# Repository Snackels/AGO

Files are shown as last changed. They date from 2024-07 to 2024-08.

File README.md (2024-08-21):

# Documentation for WRO Future Engineer 2024
by Team *YBR-AGO*



<p align="center">
  
</p>
<p align="center">
<b>By Yothinburana School Robot Club</b>
</p>
<br><br><br><br>

## Our works (Youtube Links): 
Without obstacle
**https://youtu.be/OX0P1ySq7O0?si=p41OlnyZ8GQXAvJI**

In this round, our strategy is to map the distance between the robot and the wall to be 30 CM. To start the robot, we place it on the track. Then we will open the switch to turn the robot on. After the switch is pressed, all servos will return to default position to ensure that the robot has the same value everytime. After that we will press the button at the back of our robot to start it. The ultrasonic servo will turn to the right to keep robot away from the wall. The robot will walk straight until the light sensors see the blue and red line on each corner of the track. The red sensor is used for detecting the blue line which indicate that the robot need to turn left. While blue sensor is used for both blue and red line. If the robot sees the red line first, it will turn right. We count the color line for 12 times to make sure that the robot has completed 3 laps around the track. After that line we will use timer to drive into parking position.

With obstacle

<br>

### This Github repository contains:
  - [About our team](#about-our-team)
  - [Robot Design](#robot-design)
  - [Electric Circuit And Flowchart](#electric-circuit-and-flowchart)
  - [Program Explanation](#program-explanation)

# **About our team.**
<p align="center">
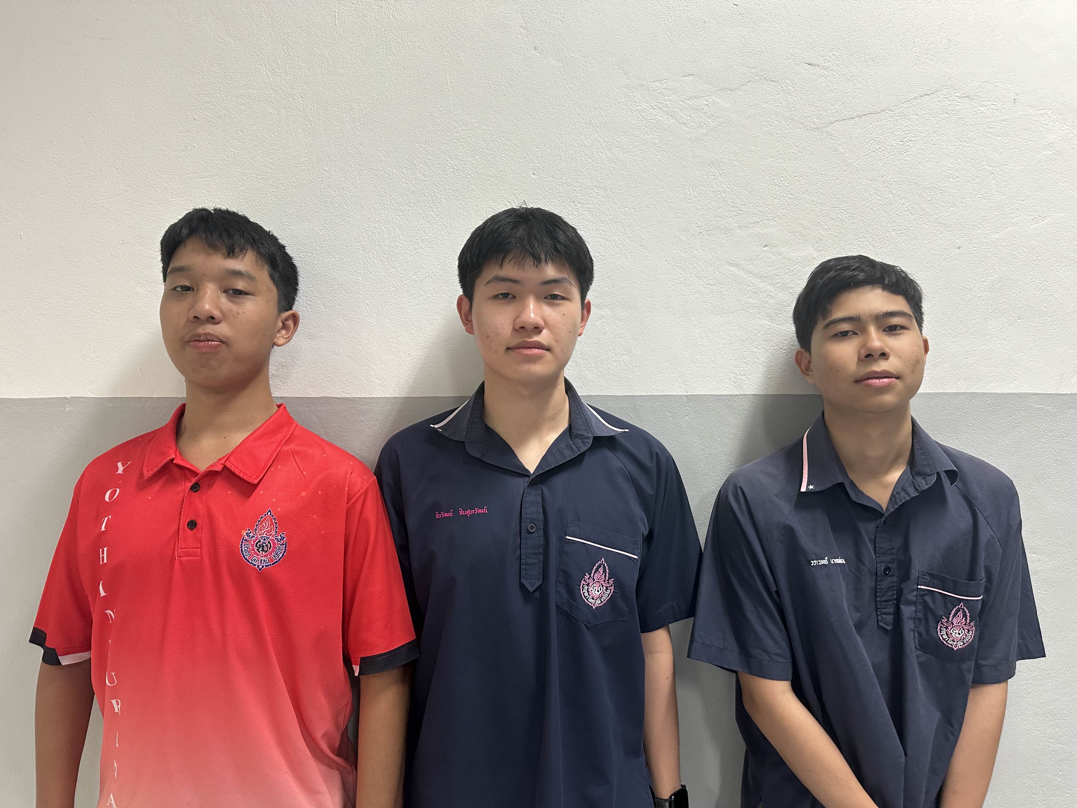
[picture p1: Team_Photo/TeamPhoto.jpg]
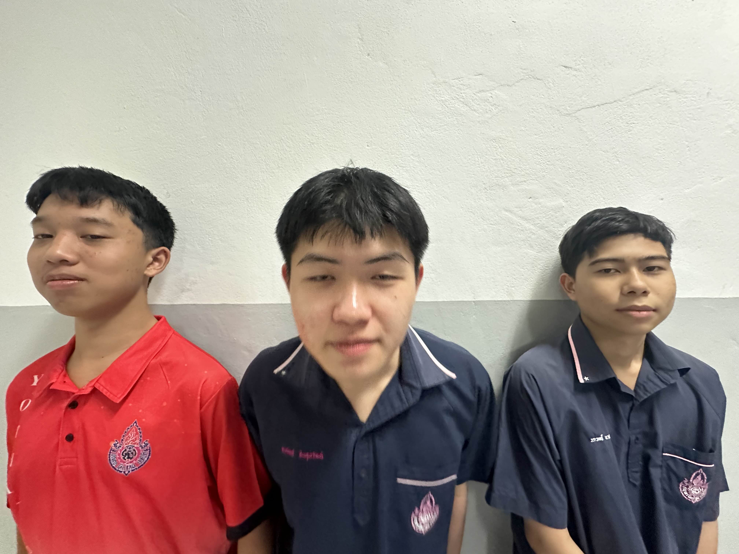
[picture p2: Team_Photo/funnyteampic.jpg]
   
</p>
<p align="center">

*YBR-AGO* comprises three students from Yothinburana School. Our team consists of two members from year 11 and one from year 10. Last year, Vichaiwat and Vorawet secured first place in Thailand national stage with team YBR-GPA4.0 while Chaiwat came in second with the team YBR-BOO. We all made it into international round as Thailand representative. Sadly, Vichaiwat and Vorawet in team called Sunflower secured 7th place and Chaiwat in Zenith secured the 8th. Now we know what we should do to prevent that from happening again and try our best to win that first place.

Here are the team members from left to right.

1. Vichaiwat Koonsap, 16 years old.

2. Chaiwat Chinsupawat, 15 years old.

3. Vorawet Narkglom, 16 years old.

# **Robot Design.**
### The Robot

Designing a robot for this competition is sometimes hard. We need to design it to be compact, lightweight, durable, and have all the functions we need. The robot must be four-wheeled with a steering function on either front or back wheel, which is why we need to be careful to pick the components. After we select all the components we need, then we think about how to put them all together. We came up with using Lego Technic parts. We spent a lot of time designing it to be within the size regulation. 

Designing a robot using Lego parts is also not easy since we need to think about everything. Every part we put in includes weight, which makes the robot slower. We failed a few times before coming up with the design we use now. After finishing designing, we combined it with other components to see the result. he robot's color also shouldn't be green and red since the camera can confuse it with the obstracle.

For the design, we placed the gyro around the middle-top of the robot to get the most accurate output, while the camera was positioned at the front of the gyro to detect objects quickly.

Our robot has two servos, one on the bottom front and one on the top front. The bottom front servo is used to steer the wheel. Then, we added a top servo that rotates our ultrasonic. We use an ultrasonic to keep our robot out of the wall. Finally, we place our motor at the bottom back of the robot, and to ensure that it drives both wheels at the back, we use a gear differential from Lego. 

Here is what our robot looks like without the components.

<image src="https://github.com/Snackels/AGO/blob/main/Robot/3D/Robot%20render.png" width = "400">

<br>

This is how to make our robot in timelapse. It shows inside of the robot of where and how to put the motor and differential.
<div align="center">
    Robot Car Assemble
</div>

<br>

### Our robot components
  
   ### Movement Parts
   
- ## **Driving motor** : Power functions Large-motor made by LEGO™.
<image src="https://github.com/Snackels/FutureEngineer2024_YBR_AGO/blob/main/Robot/Parts/Motor.png" width = "400">
It's a simple motor, and we chose this motor because of its easy connection to our robot and its cost-effectiveness. This motor is small yet powerful. and it is the perfect size for our robot. The motor comes with a dedicated port for Lego. So, we modified it to make it able to connect to the board. 

### Electrical Specifications

| Specification | Value |
|---|---|
| Voltage | 9 V |

### Mechanical Specifications

| Specification | Value |
|---|---|
| Speed | 390 rpm  |
| Maximum torque | 40 Ncm |

<br><br>

- ## **Servo** : GEEKSERVO 2kg 360 Degrees servo.
<image src="https://github.com/Snackels/FutureEngineer2024_YBR_AGO/blob/main/Robot/Parts/Servo%201.png" width = "400">
We use this servo for steering the robot and employ an ultrasonic sensor for rotation. This servo is compatible with LEGO, making it easy and convenient to build the robot by just putting studs in the hole on the side. We like how you can connect two axles to the dual outputs on this servo so you can power two wheels or gears, or mount the servo securely inside articulated limbs and other contraptions. Additionally, the gears inside these servos will 'slip' when the blocking load is too high instead of jamming, helping avoid damage to your servos and boards.

The wires are a standard servo pinout - 
-	Red - positive
-	Brown - negative
-	Yellow - data

### Electrical Specifications

| Specification | Value |
|---|---|
| Working voltage | 3.3V~6V  |
| Rated voltage | 4.8V |
| Rated current | 200mA |
| Stall current | 700mA |
| Sliding current | 450mA |

- ## **Differential** : Technic, gear differential with inner tabs and closed center, 28 bevel teeth
<image src = "https://github.com/Snackels/FutureEngineer2024_YBR_AGO/blob/main/Robot/Parts/Gear_3%20(1).png" width = "400">
This part ensure that both wheels have the power from the motor, which makes the robot drive forward. This part has gear teeth on the side, which are connected to the gear we put on the motor earlier, and then we put 3 small gears inside the differential. The differential is attached to the main body using an axle from the wheel.

<br><br>

- ## **Wheel** : Lego 49.5 × 20 tire and 30 × 20 rim
<image src = "https://github.com/Snackels/FutureEngineer2024_YBR_AGO/blob/main/Robot/Parts/Wheel%20(1).png" width = "400">
There are a lot of wheels to select. We chose this one because of it's size. If the wheels are too small, it reduces the speed due to the lack of rotation. But if the wheels are too big, it makes the robot slower and harder to control. With the combination of the motor and the wheels, the robot can maintain the speed we can control.

<br><br>

 ### Controller
- ## **Microcontroller Board** : Arduino Mega 2560 R3
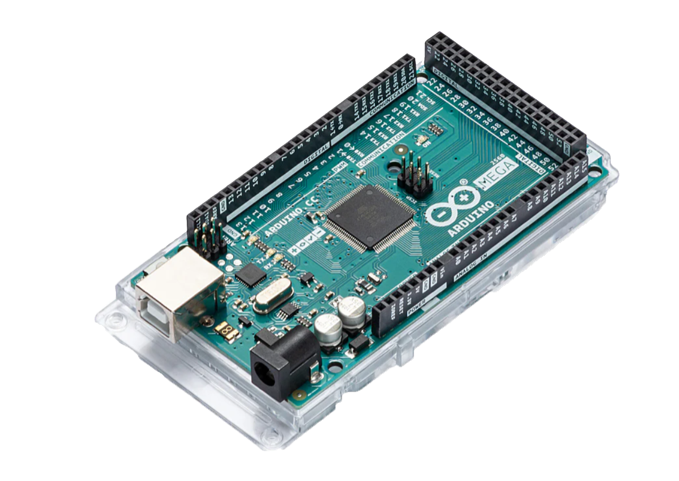
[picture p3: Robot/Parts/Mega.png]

This part is like a brain of our body. It's job is to store all the program of our robot from the computer, every components in the robot comes through here. We chose this board because of it's connection port, it contains tons of ports that we want such as 3 UART port. We used Arduino Uno last year, but the problem is there's not enough port for OpenMV and GY-25. But there's some disadvantage in this board. Because this board has a lot of connection port, it comes with weight and size. It's almost 2 times longer than the UNO. And that makes the robot long and heavy.

| Specification | Value |
|---|---|
| Microcontroller | ATmega2560 |
| Operating Voltage | 5V |
| Input Voltage (recommended) | 7-12V |
| Input Voltage (limit) | 6-20V |
| Digital I/O Pins | 54 (15 provide PWM output) |
| Analog Input Pins | 16 |
| DC Current per I/O Pin  | 20 mA |
| DC Current for 3.3V Pin | 50 mA |
| Flash Memory | 256 KB (8 KB used by bootloader) |
| SRAM | 8 KB |
| EEPROM | 4 KB |
| Clock Speed | 16 MHz |
| LED_BUILTIN | 13 |
| Length | 101.52 mm |
| Width | 53.3 mm |
| Weight | 37 g |

Additional information about UART:
UART operates by transmitting data as a series of bits, including a start bit, data bits, an optional parity bit, and stop bit(s). Unlike parallel communication, where multiple bits are transmitted simultaneously, UART sends data serially, one bit at a time. As the name reveals the protocol operates asynchronous which means that it doesn't rely on a shared clock signal. Instead, it uses predefined baud rates to determine the timing of data bits.

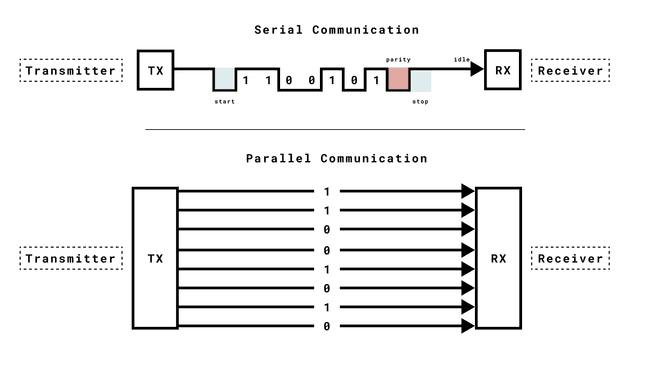
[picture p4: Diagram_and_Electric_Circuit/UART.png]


Our robot has serial1 and serial3, serial1 is connected to compass while serial3 is connected to OpenMV camera. They are connected to the UART port on the Arduino mega.

<br><br>

- ## **Sensor Shield** : Gravity IO Sensor Shield For Arduino Mega Due
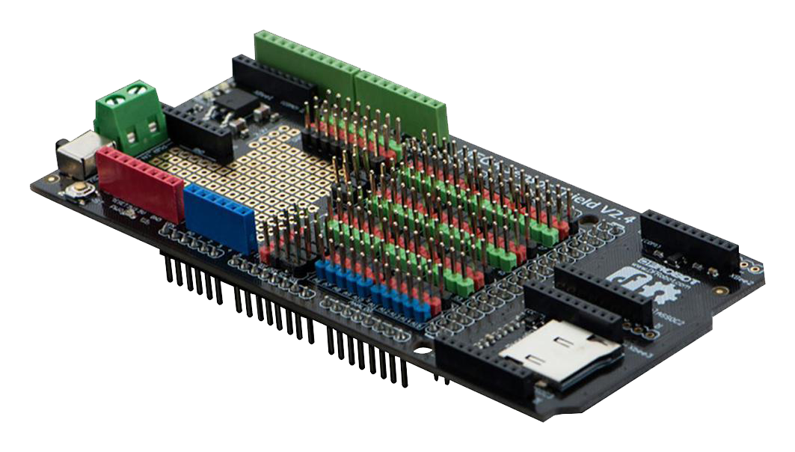
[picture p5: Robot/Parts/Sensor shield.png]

This part is an extension of the board. It is where ultrasonic, light sensors, button sensors, camera, compass, and servos go. It has alot of connection pin which can be used for each components. But with that it also come with a very long design. Make it hard to design where to place it on robot.

| Specification | Value |
|---|---|
| Compatibility | Most Arduino shields |
| Compatible Boards | Arduino Mega boards, DFRobot megaADK, Arduino megaADK |
| Extended TTL Connection Pins | Four Serial ports |
| Prototyping Area | DIP prototyping area for additional modules or components |
| Xbee Slots | 3 |
| microSD Slot | 1 |
| Power Switch | Between Arduino Mega or external power |
| Size | 125 x 57 mm (4.92 x 2.24") |

<br><br>

- ## **Motor Shield** : Gravity 2x2A Motor Shield for Arduino Twin
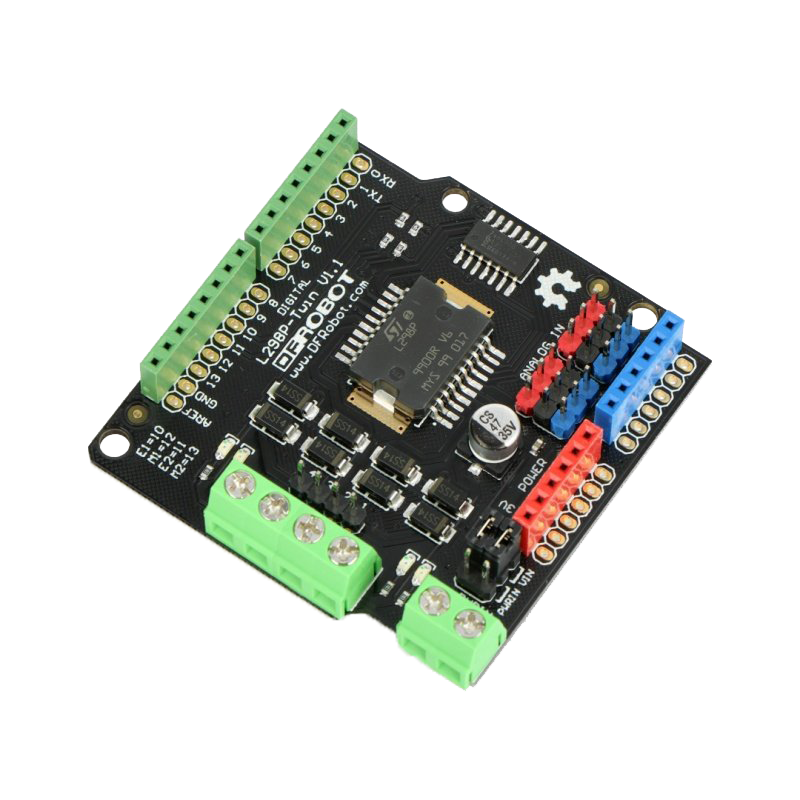
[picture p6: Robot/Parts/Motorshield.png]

This part is also an extension of the board. It makes the connection between the board and motor easier. We connect the pin with the top of sensor shield.

| Specification | Value |
|---|---|
| Motor Driven Voltage | 4.8V to 35V |
| Output Current | Up to 2A/channel |
| Total Power Dissipation | 25W (T=75℃) |
| Driven Structure | Dual full-bridge driver |
| Driven Power Port | External power terminal, or VIN from Arduino |
| Driven Output Port | 2 channel screw terminals, or male PIN headers |
| Control Port | 4 TTL compatible digital signals (Digital 10-13) |
| Operation Temperature | -25℃ to 130℃ |
| Shield Size | 56x57mm (2.20x2.24") |

<br><br>

### Power Management And Inspection
- ## **Camera** : OpenMV H7 R1
<image src="https://github.com/Snackels/AGO/blob/main/Robot/Parts/OpenMV%20cam.png" width = "400">
This component is very important for avoiding obstacle. It can detect red and green obstacle from distance to avoid crashing into it. The OpenMV also comes with it's own microcontroller. Making the robot locate and think faster when see the obstacle. The OpenMV also comes with GLCD screen at the back of it to display what the camera see. This camera can be coded with MicroPython. Additionally, this camera wires are connected with the sensor shield.

#### STM32H743VI Specifications

| Specification | Value |
|---|---|
| **Processor** | STM32H743VI ARM Cortex M7 |
| **Clock Speed** | 480 MHz |
| **SRAM** | 1 MB |
| **Flash Memory** | 2 MB |
| **I/O Voltage** | 3.3V (5V tolerant) |
| **Number of I/O Pins** | 10 |

#### Interfaces

| Specification | Value |
|---|---|
| **USB** | Full-speed USB (12 Mbps) interface |
| **μSD Card Socket** | Capable of 100 Mbps read/write |
| **SPI Bus** | Up to 80 Mbps |
| **I2C Bus** | Up to 1 Mbps |
| **CAN Bus** | Up to 1 Mbps |
| **Asynchronous Serial Bus** | Up to 7.5 Mbps |

#### Analog

| Specification | Value |
|---|---|
| **ADC** | 12-bit |
| **DAC** | 12-bit |

#### Control

| Specification | Value |
|---|---|
| **Servo Control Pins** | 3 I/O pins |
| **Interrupts and PWM** | Available on all I/O pins |

#### LEDs

| Specification | Value |
|---|---|
| **RGB LED** | Yes |
| **High Power IR LEDs** | Two 850nm |

#### Camera Module

| Specification | Value |
|---|---|
| **Default Sensor** | OV7725 |
| **Resolution** | 640x480 |
| **Modes** | 8-bit Grayscale at 75 FPS, 16-bit RGB565 (75 FPS above 320x240, 150 FPS below 320x240) |
| **Lens** | 2.8mm, M12 mount |
| **Additional Modules** | Global Shutter Camera, FLIR Lepton Adapter |

#### Power

| Specification | Value |
|---|---|
| **Battery Connector** | Compatible with 3.7V LiPo batteries |

  <br><br>

- ## **Ultrasonic sensor** : Gravity URM 09 ultrasonic distance sensor.
<image src="https://github.com/Snackels/AGO/blob/main/Robot/Parts/Ultrasonic.png" width = "400">
The ultrasonic sensor plays a vital role in guiding the robot's navigation by accurately detecting distances between the robot and potential obstacles. Its precision in measuring distances ensures that the robot can maneuver and make informed decisions to navigate its path safely and effectively, avoiding collisions and maintaining its course.

### Electrical Specifications

| Specification | Value |
|---|---|
| Supply Voltage | 3.3~5.5V DC |
| Operating Current | 20mA |

### Performance Specifications

| Specification | Value |
|---|---|
| Operating Temperature Range | -10°C to +70°C |
| Measurement Range | 2cm to 500cm (can be set) |
| Resolution | 1cm |
| Accuracy | 1% |
| Frequency | 50Hz Max |

<br><br>

- ## **7.4 voltage Lipo-Battery** : 7.4 voltage 2 cell Lipo-Battery.
<image src="https://github.com/Snackels/AGO/blob/main/Robot/Parts/Battery.png" width = "400">
The battery provides the power for our robot. This battery is very lightweight and compact to fit into the robot since the robot is very small. And it is also able to connect to our controller board. We calculated the amount of mAh that is enough to power our robot for 1-2 hours before recharged.

### Specification

| Specification | Value |
|---|---|
| 2 cells Voltage | 7.4V |
| Capacity | 1100mAh 30C |
| Charging Current | Up to 5 times the capacity (5C) |
| Connectors | JST type, easily disconnectable |

<br><br>

- ## **Light Sensor** : Virus III by Design By Sopon and ZX-03 By INEX
<image src = "https://github.com/Snackels/AGO/blob/main/Robot/Parts/Red%20sensor.png" width = "300">
Virus III
<image src = "https://github.com/Snackels/FutureEngineer2024_YBR_AGO/blob/main/Robot/Parts/Blue%20sensor.png" width = "300">
ZX-03

<br><br>

The color sensors play an important role in both rounds, as we use them for line detection. There are 2 lines with different colors in the corner of the race field, which is why we use 2 different colors of the color sensor, blue and red. The blue color sensor is used for detecting both colors, while the red color sensor is only used for the blue line.

<br><br>

- ## **GyroCompass** :GY-25
A gyro is a component that enables a robot to determine its orientation and turn in the appropriate direction. We chose this gyro sensor specifically because of how effective it is. It also comes in a very small
size to attach to our robot.

<image src = "https://github.com/Snackels/AGO/blob/main/Robot/Parts/GyroCompass.png" width = "400">

### Specification

#### Power and Communication

| Specification | Value |
|---|---|
| Power supply | 3-5V (internal low dropout regulator) |
| Used Chip | MCU+MPU6050 |
| Communication mode | Serial communication (baud 9600, 115200), IIC communication |
| Operating Current | 15 mA |

#### Angular Measurement

| Specification | Value |
|---|---|
| Angular Resolution | 0.01° |
| Direct Data | YAW ROLL PITCH |
| Measuring range of axes | -180 to +180 degrees |
| Resolution | 0.01 degrees |
| Frequency Response | 100Hz (115200bps) |
| Operating Temperature | -20 to 85°C |

<br><br>

- ## **Touch Sensor** : ZX-Switch01 by INEX
This button gives us an easier way to start the robot. Since the controller board doesn't come with switches. So we found this button that could be attached to the frame outside the board using bolt. 

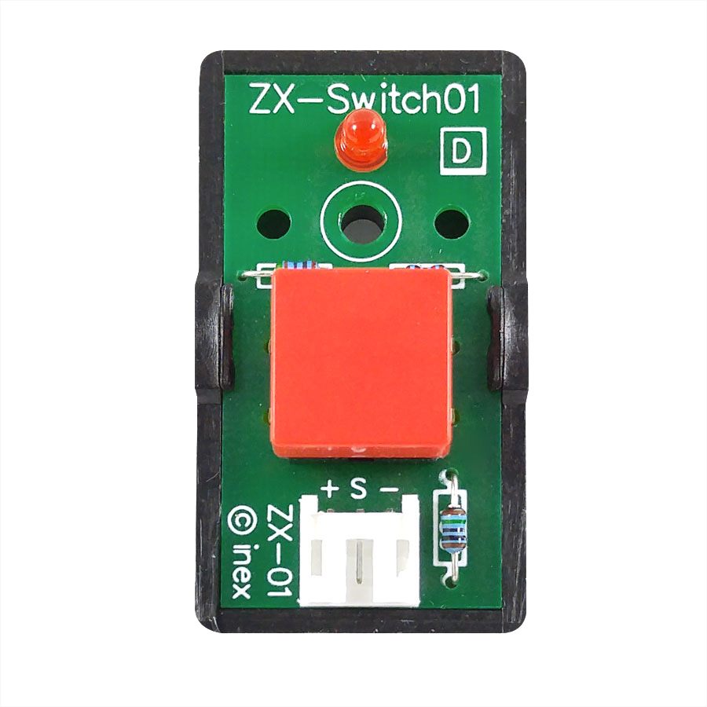
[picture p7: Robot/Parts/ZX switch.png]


<br><br>

- ## **On/Off Switch** : SPST ON/OFF Switch 2 Pin Rocker Switch DC 125/250V
This switch is for cutting the power from the battery to the robot. The regulation states that before starting the robot, the power must be cut off. That's when this switch came in. To use this switch we solder red wire(Positive pole) to the switch on 1 side for input. Then another solder red wire for output on the opposite side. You can put the black wire(Negative pole) straight into the step down. When the switch is turned on, the power from the battery will direct into the stepdown and then the robot. 

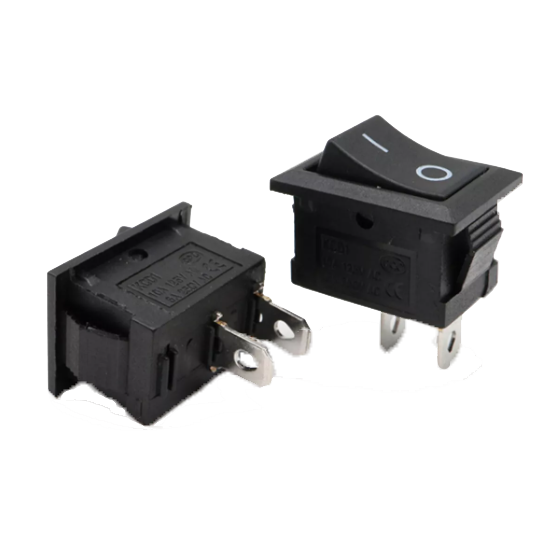
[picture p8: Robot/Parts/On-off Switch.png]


<br><br>

- ## **Step-down** : HW-360 V6.0
This is a step-down DC-DC module. It comes with a status indicator light, a display screen that shows the voltage meter, and self-calibration of the voltage meter. The electrical voltage has an error of 0.05 V, with a measuring range of 0–40 V. We need this step down to show us how long until we need to recharge the battery.

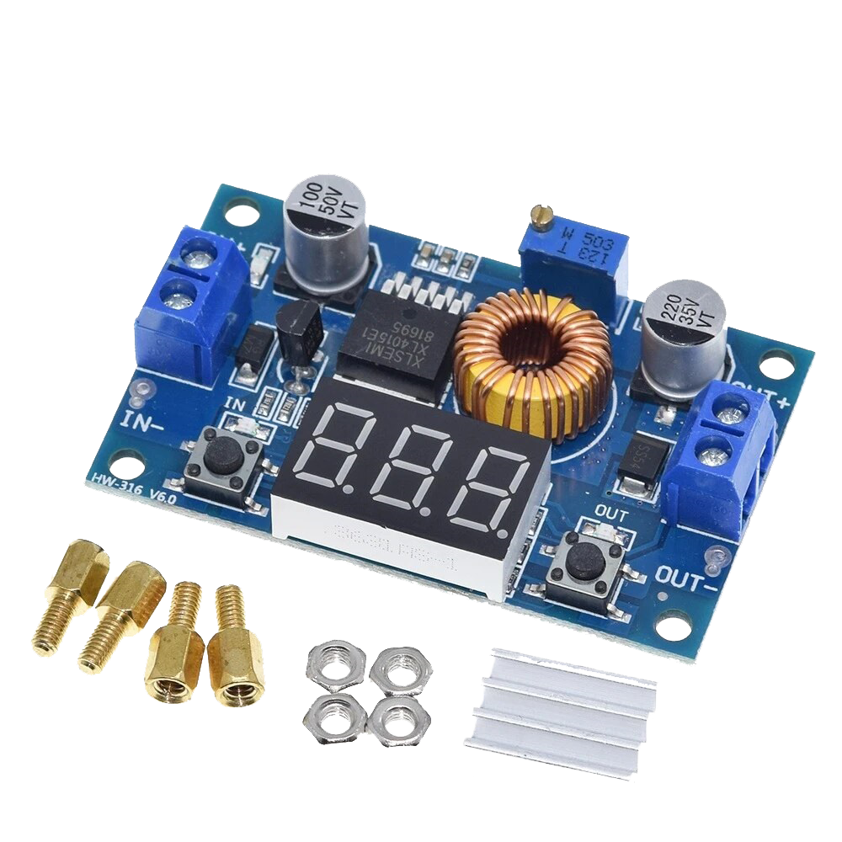
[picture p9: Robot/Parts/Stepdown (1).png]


<br><br>

### Specification

#### Input

| Specification | Value |
|---|---|
| Input voltage | DC 4.0 ~ 38V |

#### Output

| Specification | Value |
|---|---|
| Output voltage | DC 1.25V ~ 36V continuously adjustable |
| Output current | Max 5A |
| Output power | Up to 75W |

#### Measurements

| Specification | Value |
|---|---|
| Voltmeter error | ± 0.05V |
| Measure range | 0 ~ 40V |

#### Performance

| Specification | Value |
|---|---|
| Conversion efficiency | Up to 96% |
| Load regulation | S (I) ≤ 0.8% |
| Voltage Regulation | S (u) ≤ 0.8% |

<br><br>

**This is 3D model of our robot to show what our robot looks like with the components.**
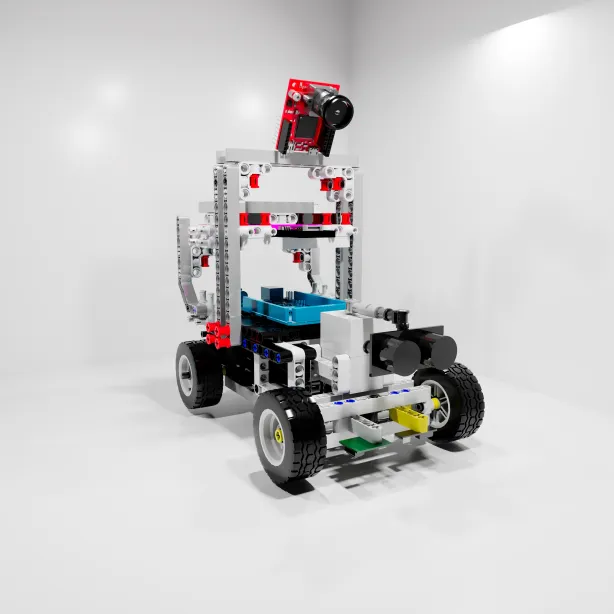
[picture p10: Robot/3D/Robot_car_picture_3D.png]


# **Electric Circuit And Flowchart**

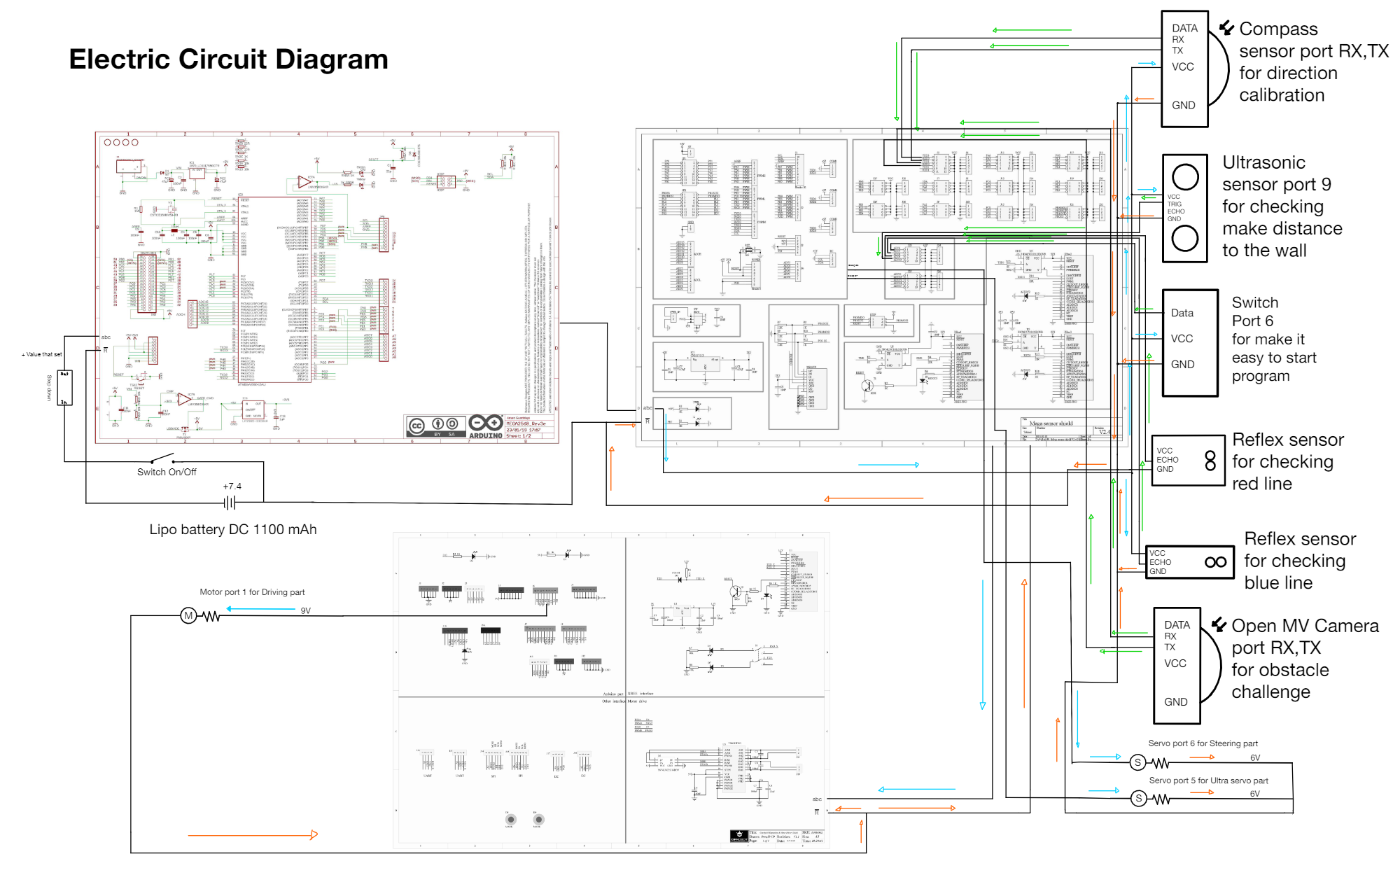
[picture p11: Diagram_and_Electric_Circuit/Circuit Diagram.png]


This is the electric diagram of our robot, showing where the wires go from the components to the board.

<br><br>

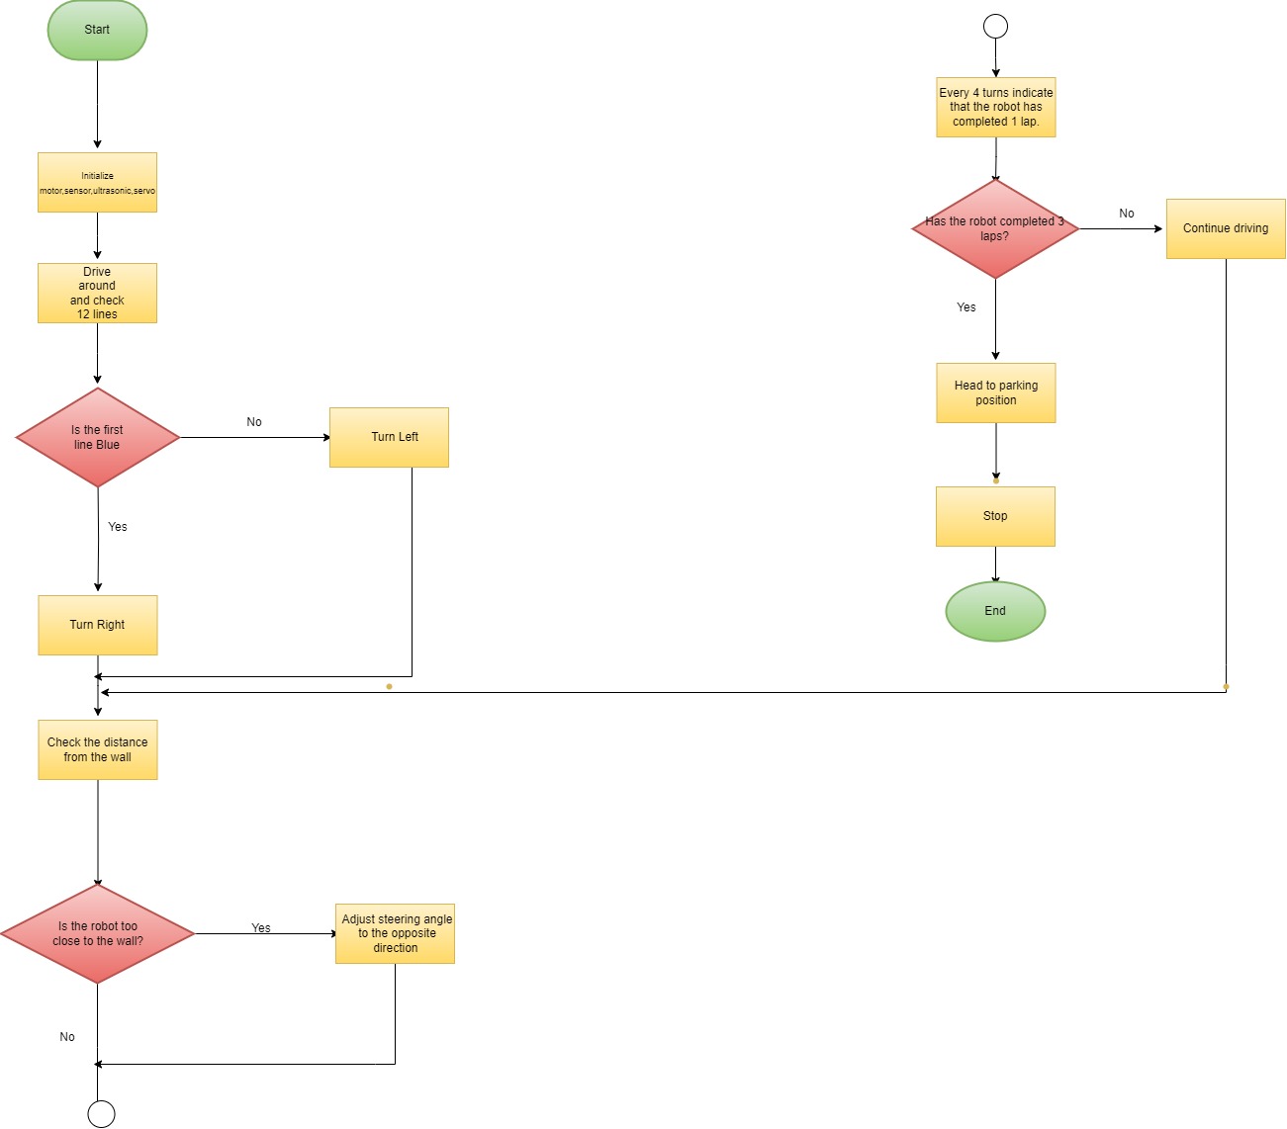
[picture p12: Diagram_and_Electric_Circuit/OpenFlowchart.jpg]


Our robot open challenge flowchart. In this round, our robot must complete 3 laps around the track within 3 minutes.

<br><br>

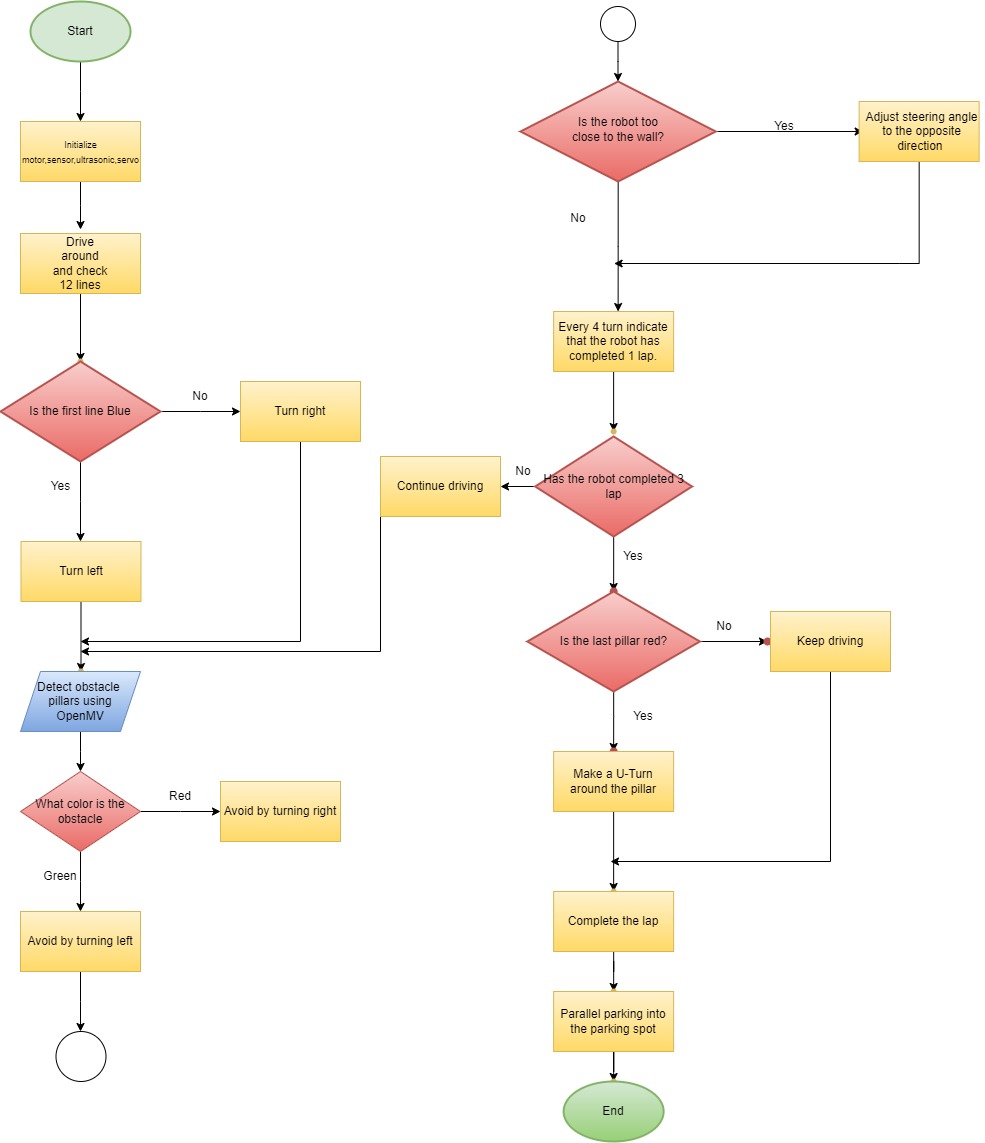
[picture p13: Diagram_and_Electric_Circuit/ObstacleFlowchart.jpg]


This flowchart shows how our robot works in obstacle challenge. 

<br><br>

 # **Program Explanation**

We have developed two programs for our upcoming competition. Each program is designed for a different round - the open challenge and the obstacle challege. The first program includes two subprograms that are also included in the program for the obstacle challenge. Each subprogram is made up of a main program and a function. 

### First Section [Open Challenge]
```c++
#include "Mapf.h"
#include <Servo.h>
#include <PID_v2.h>
```
In our program, we begin by including several libraries. One such library is Mapf.h, which extends the Arduino map() function and provides floating point reading from function mapf() and changes any ADC resolution input reading to any voltage output with mapf_ADC(). Another library we include is servo.h, which enables our controller boards to control a variety of servo motors. This library is capable of controlling a great number of servos. Additionally, we use PID_v2.h, which is a PID controller that seeks to keep some input variable close to a desired setpoint by adjusting an output. The way in which it does this can be 'tuned' by adjusting three parameters (P, I, D).

### Second Section [Open Challenge]
```c++
Servo servo1;
Servo servo2;

//motor
/**set control port**/
const int E1Pin = 10;
const int M1Pin = 12;
/**inner definition**/
typedef struct {
  byte enPin;
  byte directionPin;
} MotorContrl;

const int M1 = 0;
const int M2 = 1;
const int MotorNum = 1;

const MotorContrl MotorPin[] = { E1Pin, M1Pin };

const int Forward = LOW;
const int Backward = HIGH;

// Servos
int const Steer_Servo = 25;
int const Ultra_servo = 26;
// Ultrasonic
int const Ultra = A9;
int fDistance;
// Light sensor
int const Red_sen = A7;
int const Blue_sen = A8;
// Button
int const Button = A6;
//Compass Variable
float pvYaw, pvRoll, pvPitch;
uint8_t rxCnt = 0, rxBuf[8];
//PID
PID_v2 CompassPID(0.6, 0, 0.025, PID::Direct);
//Field config
char TURN = 'U';
long detect_line_timer;
int LineCounter = 0;
int compass_offset = 0;
int LineDetect = 0;
```
This section declares the ports for each component. We start by setting the control port for the motor. Next, we create a structure that controls the motor and its associated pins. After that, we declare the servo ports for both the steering and ultrasonic servos. Then, we specify the pins for the ultrasonic sensor, light sensors, and button sensor.

Following that, we declare variables for the compass: `pvYaw, pvRoll, and pvPitch` to store compass data. `rxCnt` is a counter for receiving data, and `rxBuf` is a buffer (array) for storing the received data.

Finally, this part of the code uses the PID_v2 library to help the robot drive straight by employing PID (Proportional-Integral-Derivative) control to correct for oversteering. The last section defines the field configuration, which will be used later in the program.

### Third Section [Open Challenge]
```c++
void setup() {
  Serial.begin(115200);
  CompassPID.Start(0, 0, 0);
  CompassPID.SetOutputLimits(-180, 180);
  CompassPID.SetSampleTime(10);
  pinMode(Steer_Servo, OUTPUT);
  pinMode(Ultra_servo, OUTPUT);
  pinMode(Ultra, INPUT);
  pinMode(Red_sen, INPUT);
  pinMode(Blue_sen, INPUT);
  pinMode(Button, INPUT);
  initMotor();
  //First Value
  fDistance = getDistance();
  while (!Serial)
    ;
  servo1.attach(Ultra_servo, 500, 2400);
  servo2.attach(Steer_Servo, 500, 2500);
  ultra_servo(0, 'R');
  steering_servo(0);
  while (analogRead(Button) > 500)
    ;
  zeroYaw();
  while (analogRead(Button) <= 500)
    ;
}
```
This section is about the "Void Setup" part of our program. The first line is `Serial.begin(115200);`, this function is a standard instruction in Arduino programming. It initializes serial communication between the Arduino board and a connected computer. Then, we initialize the PID(Proportional-Integral-Derivative) controller that declared in the earlier section.

The next step is to use the SetOutputLimit function, which allows us to define the compass's limits. Normally, a compass can rotate 360 degrees. But we changed that range into -180 to 180 degrees to make it easier to control. Following that, we use the SetSampleTime function to specify how frequently the PID controller will perform its calculations and apply control actions. In our code, we've configured it to run every 10 units of time. The subsequent lines involve using the pinMode function, which is a fundamental part of Arduino programming. It's used to set up the behavior of the component pins on an Arduino board. In our case, we set the servos as output, the ultrasonic sensor, light sensors, and button sensor as input.

`fDistance` is a short for first distance. We put it in void setup to measure the distance between the ultrasonic and the wall at the start of the program. And we use that data to add it into a function called `getDistance`.

Next line `while (!Serial);` is used to wait for the Serial communication to be established. It loops until the Serial interface is ready.

The `servo.attach` is a command that attach the servo number to the pin. And the numbers specifies the minimum and maximum pulse widths of the servo. This sets up the servo to respond to commands within this range.

The "steering" and "ultra servo" parts are set to 0 because, at the program's start, we need the servos to be in their initial positions before any movement. But the difference is "ultra servo" has letter "R" inside which indicate the side where we want the servo to turn at the when the robot start.

As for `analogRead(Button)`, it corresponds to our button. When the value obtained from analogRead(3) is more than 500, it means that the button has been pressed. In response, the compass is set to a zero yaw position. If the button is not pressed, the robot remains in its current state without making any adjustments.

### Fourth Section [Open Challenge]
```c++
void loop() {
  while (analogRead(Button) > 500) {
    getIMU();
    Color_detection();
    // Serial.print("red");
    // Serial.print(analogRead(Red_sen));
    // Serial.print("blue");
    // Serial.println(analogRead(Blue_sen));
    motor(100);
    start();
    //Serial.println(pvYaw);
    steering_servo(CompassPID.Run(pvYaw + ((getDistance() - 30)) * ((float(TURN == 'R') - 0.5) * 2)));
    ultra_servo(pvYaw, TURN);
    if (LineCounter >= 12) {
      long TimerLine = millis();
      while (millis() - TimerLine < 920) {
        getIMU();
        Color_detection();
        steering_servo(CompassPID.Run(pvYaw + ((getDistance() - 30)) * ((float(TURN == 'R') - 0.5) * 2)));
        ultra_servo(-pvYaw, TURN);
      }
      motor(0);
      while (true) {
      }
    }
  }

  while (analogRead(Button) <= 500) {
    motor(0);
  }
  while (analogRead(Button) > 500)
    ;
  while (analogRead(Button) <= 500)
    ;
}
```
In this section, we start with a button press. When the button is pressed, the robot retrieves data from the IMU (Inertial Measurement Unit) through the function `getIMU`. Subsequently, the robot begins line detection using the `Color_detection` function. 

After that, we set the speed of the robot to be 100. Next line is a function called start. It is used to handle the adjustment of the robot’s steering and ultrasonic sensor based on its current state and sensor readings, provided LineDetect is not 1. 

Now, the main program we also use a function called `steering servo`. Inside that function it contains a formula of how we walk. Here is a quick break down, we start off with `Compass.PID.Run`. This code was a part of the library PID.v2 that applied a PID formula into compass. Then inside the bracket it contains the addition of variable `pvYaw` and a function called `getDistance` minus by the distance away from the wall. And outside that bracket we multiply it by another bracket that contain `float(Turn == 'R') - 0.5)*2);`. Turn is a variable we declared at the beginning and R is a variable which indicate the side in this case, its right. If `(Turn == 'R')` is equal to 1, then we subtract it with 0.5 and then multiply with 2. The result will be 1 that mean the robot need to turn right. But in another case it isnt turn right. Then the `(Turn == 'R')` would equal to 0. When we subtract with 0.5 and multiply with 2, the result will be -1. Meaning if the robot turn right the value will be 1 and if turn left it will be -1. In summary, this line of code adjusts the steering of the robot using a PID controller to maintain within direction, factoring in both the distance measurement and the direction of turning.

On this line is another function called `ultra_servo` which use `pvYaw` and `TURN` to control which direction the servo is turning toward. After that then there's a logic "if". Inside if theres a function called `line detection` which is for detecting red and blue line on race track by using light sensors. So if the robot detect equal or more than 12 lines that mean the robot has completed 3 laps around the track and is about to end it's program. Next line we declared a variable called `TimerLine` equals to millisec. And while millisec minus with `TimerLine` is less than 920. Then we get the IMU value and use a `Color_detection` function. Also we used the same servo formula as before to keep the robot straight into the stop position without crashing into walls. Then we end the program with motor speed to 0. 

Additionally we added another line of code to stop the robot program by pressing button to stop the motor from running. And to keep it running again you must reset your robot.

<br><br>

### First Section [Obstacle Challenge]
```c++
#include "Mapf.h"
#include <Servo.h>
#include <PID_v2.h>
```
In this section, there's nothing to explain about since it mirror with open challenge.

### Second Section [Obstacle Challenge]
```c++
Servo servo1;
Servo servo2;

//motor
/**set control port**/
const int E1Pin = 10;
const int M1Pin = 12;
/**inner definition**/
typedef struct {
  byte enPin;
  byte directionPin;
} MotorContrl;

const int M1 = 0;
const int M2 = 1;
const int MotorNum = 1;

const MotorContrl MotorPin[] = { E1Pin, M1Pin };

const int Forward = LOW;
const int Backward = HIGH;

// Servos
int const Steer_Servo = 25;
int const Ultra_servo = 26;
// Ultrasonic
int const Ultra = A9;
int fDistance;
// Light sensor
int const Red_sen = A7;
int const Blue_sen = A8;
// Button
int const Button = A6;
//Compass Variable
float pvYaw, pvRoll, pvPitch;
uint8_t rxCnt = 0, rxBuf[8];
//PID
PID_v2 CompassPID(0.6, 0, 0.025, PID::Direct);
//Field config
char TURN = 'U';
long detect_line_timer;
int LineCounter = 0;
int compass_offset = 0;
int LineDetect = 0;
//Camera Variable
static int GreenBlobX = -1;
static int GreenBlobY = -1;
static int GreenBlobHeight = -1;
static int RedBlobX = -1;
static int RedBlobY = -1;
static int RedBlobHeight = -1;
char ColorChecker = 'U';  // Default value

char buffer[128];  // Buffer to hold incoming data
char *string[5];   // Array to hold token pointers
char *ptr = NULL;  // Pointer to current token
//Avoidance Variable
float YDistance;
float XDistance;
bool FoundBlock = false;
float CalculateAvoidance = 0;
char LatestBlock;

//Return Variable
float GInitialY = 0;
float GInitialX = 0;
float RInitialY = 0;
bool blockDodged = false;
bool returnvalue = false;
long dodgeTime;
int final_value;
```
In this section, most of the code are the same. But we added a few more variable for our camera to help mapping the obstacle pillars. Let's start with `GreenBlob` and `RedBlob`. In the program above, there are 3 different variable for each pillar color. Those variable are used to locate the obstacle pillar by measuring the size. It also helps with the case that if there are 2 pillars, this can map the size of the pillars to see which one is bigger and the bigger being closer.

Next line is `ColorChecker`. It is used to detect the color of the pillar. In this case there are only 2 colors being red and green. Following line, there is a char variable called `buffer` which is used for holding the incoming data within 128 letters. Next is char `*string` which defines an array of 5 pointers to char. And next is char `*ptr` is used to declares a pointer to char and initializes it to NULL.

Now, we are here with variable we use to avoid the obstacle. First is `YDistance` which is used to measure the distance between the robot and the obstacle in Y axis. And `XDistance` is used to measure from X axis. After that, there's a boolean logic when `FoundBlock` is equal to false. The float `CalculateAvoidance` is set to 0 because it will be changed later in the program. And next char is used to detect the last block to decide if it need to perform a U-Turn around the red pillar or it can just drive pass the green one. 

Finally, this is the part where we return the variable value. 

### Third Section [Obstacle Challenge]
```c++
void setup() {
  Serial.begin(19200);
  Serial3.begin(19200);
  CompassPID.Start(0, 0, 0);
  CompassPID.SetOutputLimits(-180, 180);
  CompassPID.SetSampleTime(10);
  pinMode(Steer_Servo, OUTPUT);
  pinMode(Ultra_servo, OUTPUT);
  pinMode(Ultra, INPUT);
  pinMode(Red_sen, INPUT);
  pinMode(Blue_sen, INPUT);
  pinMode(Button, INPUT);
  initMotor();
  servo1.attach(Ultra_servo, 500, 2400);
  servo2.attach(Steer_Servo, 500, 2500);
  ultra_servo(0, 'R');
  steering_servo(0);
  while (analogRead(Button) > 500)
    ;
  zeroYaw();
  while (analogRead(Button) <= 500)
    ;
}
```
This section also mirror with the open challenge. But with a few adjustment in the `serial.begin`. The `serial` is for connecting with the compass while `serial3` is for connecting with the camera.

### Fourth Section [Obstacle Challenge]
```c++
void loop() {
  while (analogRead(Button) > 500) {
    BobDetection();
    CalculateAvoidance = Avoidance_calculation();
    if ((!blockDodged && CalculateAvoidance != 0) || (FoundBlock == true && CalculateAvoidance != 0)) {
      blockDodged = true;  // Mark the block as dodged
      final_value = CalculateAvoidance;
    }

    if ((blockDodged && CalculateAvoidance == 0) || (blockDodged && FoundBlock == false)) {
      blockDodged = false;
      returnvalue = true;
    }

    if (returnvalue == true) {
      float returncalculation = (asin(sqrt(sq(GInitialX) + sq(GInitialY)))) * -2;
      while ((getDistance() > GInitialX +3) || (getDistance() < GInitialX - 3)) {
        final_value = returncalculation;
      }
      returnvalue = false;
      GInitialY = 0;
      GInitialX = 0;
      RInitialY = 0;
      blockDodged = false;
    }
    // Serial.print(LatestBlock);
    Serial.print(" ");
    Serial.println(CalculateAvoidance);
    motor(100);
    steering_servo(final_value);
  }
  while (analogRead(Button) <= 500) {
    motor(0);
  }
  while (analogRead(Button) > 500)
    ;
  while (analogRead(Button) <= 500)
    ;
}
```
In this section, we begin with button. If the button is pressed the program will start. After the program start, we utilize a function called `BobDetection`. This function is for detecting the obstacle block. Then we declare that `CalculateAvoidance` is equal to `Avoidance_calculation` function.

In this line, there's if logic. First, if `blockDodged` and `CalculateAvoidance` is not 0 or the robot `foundblock` then `calculateavoidance` is not 0. In this logic, we also declared that `blockdodged` is true meaning that we are marking that pillar. But in another case, if `blockDodged` and `CalculateAvoidance` is not 0 or the robot didn't dodged the block or found any pillar. Then we marked that `blockdodged` is false and then return the value. Following up is if `returnvalue` is true, we will calculate `returncalculation` by calculating `(asin(sqrt(sq(GInitialX) + sq(GInitialY)))) * -2;`. And while getDistance is more than `GInitialX` plus by 3 or less than `GInitialX` minus by 3. Then the `final_value` is equal to `returncalculation`. After, we return the value.

This is where the code is used to drive the robot. We used the function called `steering_servo` and we put the `final_value` we calculated earlier inside to drive the robot forward and avoid hitting the obstacle. Finally, the program can ended with the button sensor being pressed.

### Function 

This is all the function of our program.

### `Set motor direction`
```c++
void setMotorDirection(int motorNumber, int direction) {
  digitalWrite(MotorPin[motorNumber].directionPin, direction);
```
- **Description**: This program is use to set the direction of the motor. There's 2 input. First is the motor port connection. Second is the direction the robot is heading.

### `Set motor speed`
```c++
inline void setMotorSpeed(int motorNumber, int speed) {
  analogWrite(MotorPin[motorNumber].enPin, 255.0 * (speed / 100.0));
```
- **Description**: This function is for controlling the speed of the motor by inputting motor port connection and speed you want.

### `Motor`
```c++
void motor(int speed) {
  if (speed > 0) {
    setMotorDirection(M1, Forward);
    setMotorSpeed(M1, speed);
  } else {
    setMotorDirection(M1, Backward);
    setMotorSpeed(M1, speed * -1);
  }
}
```
- **Description**: This function is very important as we use it to control our motor by using the first two function. There's only 1 input in this function which is the speed. When the speed is positive, the robot will be driving forward. But if it's negative, the robot will do the opposite.

### `Initiate motor`
```c++
void initMotor() {
  int i;
  for (i = 0; i < MotorNum; i++) {
    digitalWrite(MotorPin[i].enPin, LOW);

    pinMode(MotorPin[i].enPin, OUTPUT);
    pinMode(MotorPin[i].directionPin, OUTPUT);
  }
}
```
- **Description**: This `initMotor` function initializes the motor control pins for a number of motors.

### `Wrap value`
```c++
int wrapValue(int value, int minValue, int maxValue) {
  int range = maxValue - minValue + 1;
  if (value < minValue) {
    value += range * ((minValue - value) / range + 1);
  }
  return minValue + (value - minValue) % range;
}
```
- **Description**: Use to ensures that a value remains within specified minimum and maximum bounds. If the value exceeds these bounds, it wraps around to the other end of the range.

### `Zero yaw`
```c++
void zeroYaw() {
  Serial1.begin(115200);
  delay(100);
  // Sets data rate to 115200 bps
  Serial1.write(0XA5);
  delay(10);
  Serial1.write(0X54);
  delay(100);
  // pitch correction roll angle
  Serial1.write(0XA5);
  delay(10);
  Serial1.write(0X55);
  delay(100);
  // zero degree heading
  Serial1.write(0XA5);
  delay(10);
  Serial1.write(0X52);
  delay(100);
  // automatic mode
}
```
- **Description**: This function is for the compass.It is used to set compass into 0 degree. It's essential to ensure consistent behavior each time the robot drives.

### `Get IMU`
```c++
bool getIMU() {
  while (Serial1.available()) {
    rxBuf[rxCnt] = Serial1.read();
    if (rxCnt == 0 && rxBuf[0] != 0xAA) return;
    rxCnt++;
    if (rxCnt == 8) {  // package is complete
      rxCnt = 0;
      if (rxBuf[0] == 0xAA && rxBuf[7] == 0x55) {  // data package is correct
        pvYaw = (int16_t)(rxBuf[1] << 8 | rxBuf[2]) / 100.f;
        pvPitch = (int16_t)(rxBuf[3] << 8 | rxBuf[4]) / 100.f;
        pvRoll = (int16_t)(rxBuf[5] << 8 | rxBuf[6]) / 100.f;
        pvYaw = wrapValue(pvYaw + compass_offset, -179, 180);
        return true;
      }
    }
  }
  return false;
}
```
- **Description**: This function is used to get data from the IMU (Inertial Measurement Unit). It processes incoming data in a specific format, extracts yaw information, and ensures it stays within a defined range. It returns `true` when it successfully processes valid data and `false` otherwise.

### `Ultrasonic Servo`
```c++
void ultra_servo(int degree, char mode_steer) {
  int middle_degree = 0;
  if (mode_steer == 'F') {
    middle_degree = 142;
  } else if (mode_steer == 'R' || mode_steer == 'U') {
    middle_degree = 70;  //45
  } else if (mode_steer == 'L') {
    middle_degree = 210;
  } else {
  }
  servo1.write(mapf(max(min(middle_degree + degree, 225), 45), 0, 270, 0, 180));
}
```
- **Description**: This function controls a servo motor's position based on the desired degree and the mode_steer parameter, which determines the middle degree position. It ensures that the servo's position is within the valid range for servo control.

### `Steering servo`
```c++
void steering_servo(int degree) {
  servo2.write((90 + max(min(degree, 48), -48)) / 2);
}
```
- **Description**: This function controls a servo motor's position based on the desired degree. It ensures that the servo's position is within a valid range for servo control.

### `Get distance`
```c++
float getDistance() {
  return min(mapf(analogRead(Ultra), 0, 1023, 0, 500), 50);
}
```
- **Description**: This function is used to measure the distance between the wall and the robot using an ultrasonic sensor. It provides a simple way to obtain distance data.

### `Color detect`
```c++
void Color_detection() {
  int blue_value = analogRead(Blue_sen);
  if (TURN == 'U') {
    int red_value = analogRead(Red_sen);
    if (blue_value < 679 || red_value < 329) {
      int lowest_red = red_value;
      long color_window = millis();
      while (millis() - color_window < 100) {
        int red_value = analogRead(Red_sen);
        if (red_value < lowest_red) {
          lowest_red = red_value;
        }
      }
      if (lowest_red > 329) {
        TURN = 'L';
        compass_offset += 90;
      } else {
        TURN = 'R';
        compass_offset -= 90;
      }
      detect_line_timer = millis();
      LineCounter++;
      LineDetect = 1;
    }
  } else {
    if (millis() - detect_line_timer > 1300) {
      if (blue_value < 679) {
        if (TURN == 'R') {
          compass_offset -= 90;
        } else {
          compass_offset += 90;
        }
        detect_line_timer = millis();
        LineCounter++;
        LineDetect = 1;
      }
    }
  }
}
```
- **Description**: This function is responsible for detecting lines and making decisions about steering behavior and the TURN mode based on sensor readings and timing.

### `Start`
```c++
void start() {
  Serial.println(LineDetect);
  if (LineDetect != 1) {
    steering_servo(CompassPID.Run(pvYaw + ((getDistance() - fDistance))));
    ultra_servo(pvYaw, TURN);
  } 
```
- **Description**: This function is a part of a control loop for our robot system where sensors provide data to adjust steering and ultrasonic servos to navigate a path.

### `Block Detection`
```c++
void BobDetection() {
  static int bufferIndex = 0;
  while (Serial3.available()) {
    char byteRead = Serial3.read();  // Read byte from Serial3

    if (byteRead == '\n') {        // End of line detected
      buffer[bufferIndex] = '\0';  // Null-terminate the buffer
      bufferIndex = 0;             // Reset buffer index

      // Tokenize the buffer
      ptr = strtok(buffer, ",");
      int index = 0;
      while (ptr != NULL && index < 5) {
        string[index] = ptr;  // Store the token
        index++;
        ptr = strtok(NULL, ",");
      }

      // Ensure that there are enough tokens before accessing them
      if (index >= 4) {  // Ensure we have at least 4 tokens
        // Assuming ColorChecker is meant to be a single character
        ColorChecker = string[3][0];  // Assign single character from the token
        FoundBlock = true;

        if (ColorChecker == 'G') {
          // If ColorChecker is 'G', update GreenBlob values
          GreenBlobX = atoi(string[0]);
          GreenBlobY = atoi(string[1]);
          GreenBlobHeight = atoi(string[2]);
        } else if (ColorChecker == 'R') {
          // If ColorChecker is 'R', update RedBlob values
          RedBlobX = atoi(string[0]);
          RedBlobY = atoi(string[1]);
          RedBlobHeight = atoi(string[2]);
        }

        // Print values to Serial Monitor for debugging
        // Serial.print("GreenBlobX: ");
        // Serial.print(GreenBlobX);
        // Serial.print(" GreenBlobY: ");
        // Serial.print(GreenBlobY);
        // Serial.print(" GreenBlobHeight: ");
        // Serial.print(GreenBlobArea);
        // Serial.print(" RedBlobX: ");
        // Serial.print(RedBlobX);
        // Serial.print(" RedBlobY: ");
        // Serial.print(RedBlobY);
        // Serial.print(" RedBlobArea: ");
        // Serial.print(RedBlobArea);
        // Serial.print(" ColorChecker: ");
        // Serial.println(ColorChecker);
      } else {
        // Handle the case where there are not enough tokens
        Serial.println("Error: Not enough data tokens received.");
        FoundBlock = false;
        GreenBlobX = -1;
        GreenBlobY = -1;
        GreenBlobHeight = -1;
        RedBlobX = -1;
        RedBlobY = -1;
        RedBlobHeight = -1;
      }
    } else {
      // Store byte in buffer if not end of line
      if (bufferIndex < sizeof(buffer) - 1) {
        buffer[bufferIndex++] = byteRead;
      } else {
        // Buffer overflow protection
        bufferIndex = 0;  // Reset buffer if it overflows
        Serial.println("Error: Buffer overflow.");
      }
    }
  }
}
```
- **Description**: This function is designed to read and process data from a serial input, which is the camera. It reads incoming data byte by byte and then processes it to extract information, and updates various variables based on the received tokens.

### `Avoidance calculation`
```c++
float Avoidance_calculation() {
  if (FoundBlock == true) {

    int focalLenght = 2.8;
    int TargetHeight = 10;

    if (ColorChecker == 'G') {
      float Gdistance = (TargetHeight * focalLenght * 79) / GreenBlobHeight;
      float GDeltaX = GreenBlobX - 160;
      float Gdetected_degree = GDeltaX * 70 / 320;
      float GBlockX = Gdistance * sin(degreesToRadians(Gdetected_degree));
      if (GInitialX == 0) {
        GInitialX = getDistance();
      }
      float GBlockY = Gdistance * cos(degreesToRadians(Gdetected_degree)) - 16;
      if (GInitialY == 0) {
        GInitialY = GBlockY;
      }
      CalculateAvoidance = max(radiansToDegree(atan2(GBlockX + 9, GBlockY)), 5);
      LatestBlock = 'G';
      // BlocksTurn = 'TURN';
      // Serial.println(Gdistance);
    } else if (ColorChecker == 'R') {
      float Rdistance = (TargetHeight * focalLenght * 100) / RedBlobHeight;
      float RDeltaX = RedBlobX - 160;
      float Rdetected_degree = RDeltaX * 40 / 320;
      float RBlockX = Rdistance * sin(degreesToRadians(Rdetected_degree));
      float RBlockY = Rdistance * cos(degreesToRadians(Rdetected_degree)) - 16;
      CalculateAvoidance = min(radiansToDegree(atan2(RBlockX - 9, RBlockY)), 5);
      LatestBlock = 'R';
    }
  } else {
    CalculateAvoidance = 0;
  }
  return CalculateAvoidance;
}
```
- **Description**:  This function utilizes the OpenMV camera data to calculate the robot's optimal steering to avoid obstacles effectively. It plays a crucial role in maintaining the robot's path and avoiding collisions. The code is configured to use a specific signature and size for red and green obstacles in the OpenMV app.

### `Degree to radians calculator`
```c++
float degreesToRadians(double degrees) {
  return degrees * PI / 180.0;
}
```
- **Description**: This simple function converts angle measurements between degrees and radians, aiding in angle calculations within the code.

### `Radians to degree calculator`
```c++
float radiansToDegree(double raidans) {
  return raidans / PI * 180.0;
}
```
- **Description**: This function, as the counterpart to `degreesToRadians`, converts angles from radians to degrees, facilitating angle calculations.

### OpenMV 

Our OpenMV GLCD code.

```py
import sensor, image, time
import display
from pyb import UART

sensor.reset()
sensor.set_pixformat(sensor.RGB565)
sensor.set_framesize(sensor.QVGA)  # 320x240 max size 76,800
sensor.skip_frames(time=1000)
sensor.set_auto_gain(False)  # Must be turned off for color tracking
sensor.set_auto_whitebal(False)  # Must be turned off for color tracking
sensor.set_auto_exposure(False)

GreenThresholds = [(57, 0, -10, -128, 14, 127)]
RedThresholds = [(100, 0, 38, 127, -127, 127)]

uart = UART(3, 19200)
clock = time.clock()

# Initialize LCD using SPI Display
lcd = display.SPIDisplay()

while(True):
    clock.tick()
    img = sensor.snapshot()

    GreenBob = img.find_blobs(GreenThresholds, pixels_threshold=200, area_threshold=200, merge=True, margin=5)
    if GreenBob:
        LargestGreenBob = max(GreenBob, key=lambda b: b.area())
        img.draw_rectangle(LargestGreenBob.rect(), color=(0, 255, 0))
        img.draw_cross(LargestGreenBob.cx(), LargestGreenBob.cy(), color=(0, 255, 0))
        uart.write("%d,%d,%d,%c,    \n" % (LargestGreenBob.cx(), LargestGreenBob.cy(), LargestGreenBob.area(), "G",))

    RedBob = img.find_blobs(RedThresholds, pixels_threshold=200, area_threshold=200, merge=True, margin=5)
    if RedBob:
        LargestRedBob = max(RedBob, key=lambda b: b.area())
        img.draw_rectangle(LargestRedBob.rect(), color=(255, 0, 0))
        img.draw_cross(LargestRedBob.cx(), LargestRedBob.cy(), color=(255, 0, 0))
        uart.write("%d,%d,%d,%c,\n" % (LargestRedBob.cx(), LargestRedBob.cy(), LargestRedBob.area(), "R",))

    lcd.write(img)

    if uart.any():
        data = uart.readline()
        print("Received:", data)
```
We use this code with our OpenMV camera. It is for setting up the GLCD camera to display what the camera sees and add a box around the obstracle to make sure that the camera sees the box.

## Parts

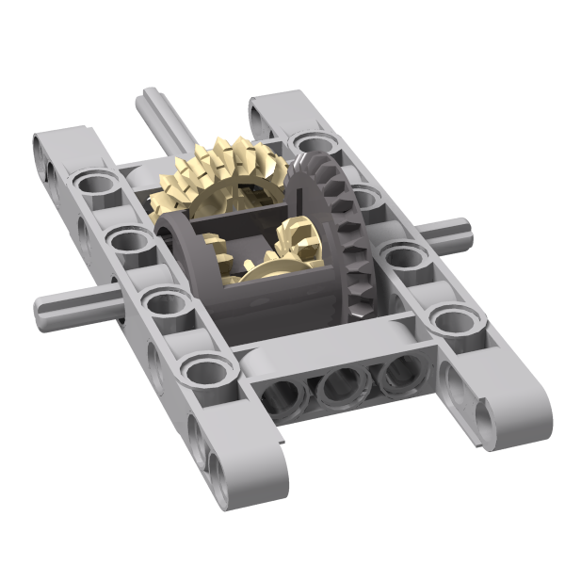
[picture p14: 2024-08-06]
Robot/Parts/Gear_3 (1).png

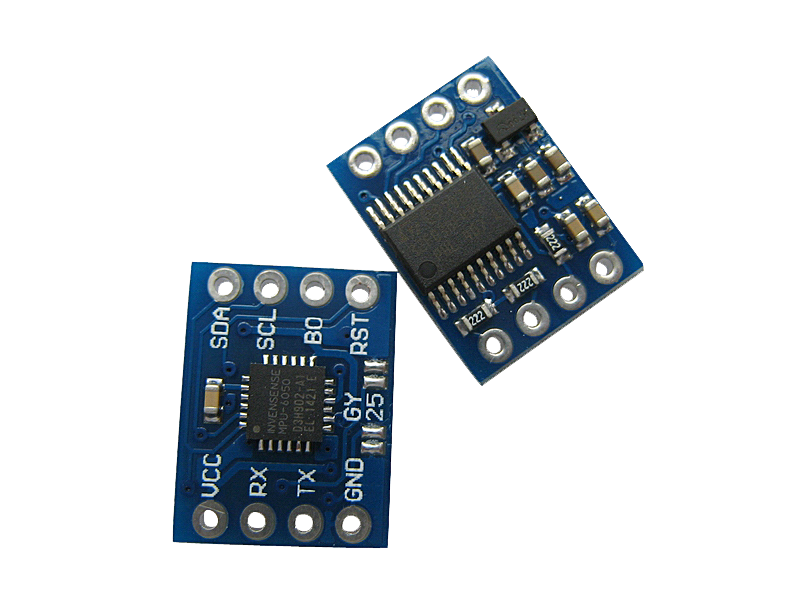
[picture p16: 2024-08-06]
Robot/Parts/GyroCompass.png

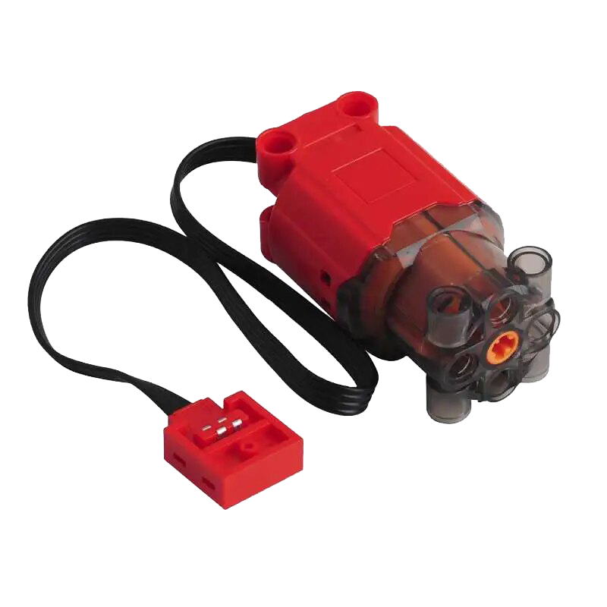
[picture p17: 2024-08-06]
Robot/Parts/Motor.png

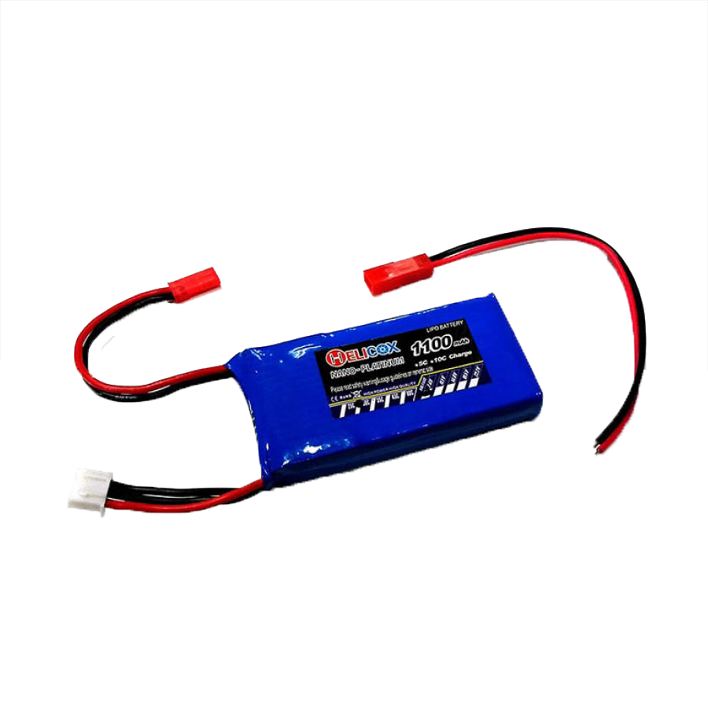
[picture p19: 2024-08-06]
Robot/Parts/Battery.png

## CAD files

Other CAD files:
Robot/3D/Mega.obj

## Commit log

2024-08-20 add UART
2024-08-20 adjust UART
2024-08-20 add circuit
2024-08-20 change circuit
2024-08-20 Fix circuit
2024-08-20 Rename Circuit.png to Circuit Diagram.png
2024-08-20 Rename Virus (1).png to Red sensor.png
2024-08-20 Rename gy25-tilt-sngle-sensor-oky3254 (1).png to GyroCompass.png
2024-08-20 Create de
2024-08-21 add obstracle flow
2024-08-21 Adjust flowchart
